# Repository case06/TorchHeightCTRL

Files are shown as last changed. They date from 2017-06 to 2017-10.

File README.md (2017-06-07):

# TorchHeightCTRL
Capacitive height-controller for the OpenSourceEcology.org TorchTable

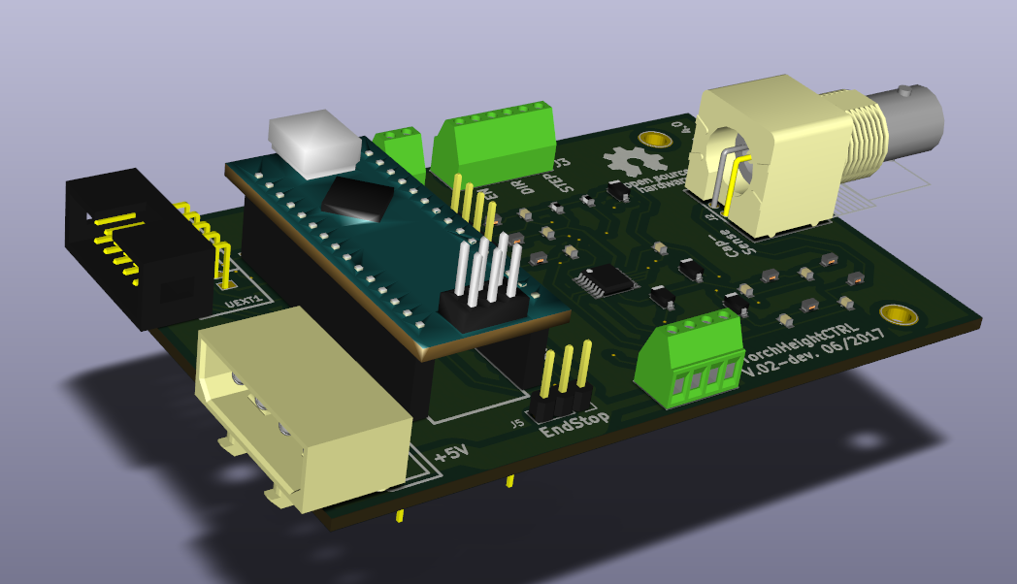
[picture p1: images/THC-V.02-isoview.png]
TorchHeightCTRL PCB
<p></p>

see also http://opensourceecology.org/wiki/CNC_Torch_Table_Height_Controller

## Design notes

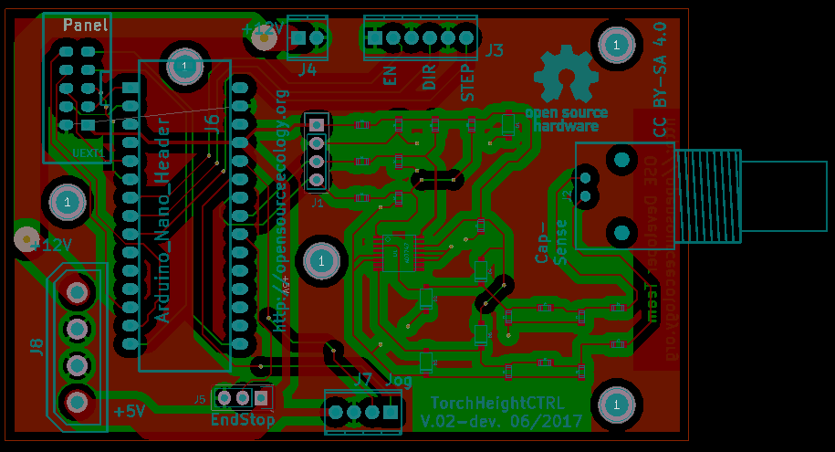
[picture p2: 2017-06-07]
images/THC-V.02-pcb.png

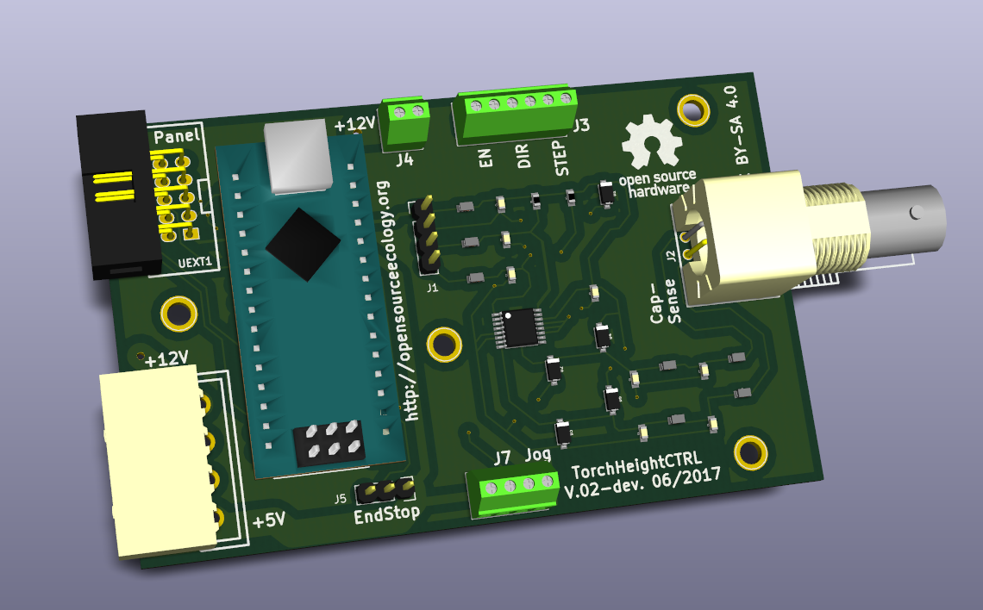
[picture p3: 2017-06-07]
images/THC-V.02-topview.png

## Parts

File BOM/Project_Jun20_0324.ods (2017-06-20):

TORCHHEIGHTCTRL02
Mouser No | Mfr. No | Manufacturer | Customer No | Description | RoHS | Lifecycle | Order Qty. | Price (EUR) | Ext.: (EUR)
78-MMSZ5233B-E3-08 | MMSZ5233B-E3-08 | Vishay |  | Zener Diodes 6.0 Volt 0.5W 5% | RoHS Compliant |  | 1 | 0,179 € | 0,18 €
71-CRCW0603J-4.7K-E3 | CRCW06034K70JNEA | Vishay |  | Thick Film Resistors - SMD 1/10watt 4.7Kohms 5% | RoHS Compliant By Exemption |  | 1 | 0,09 € | 0,09 €
571-5-146280-3 | 5-146280-3 | TE Connectivity |  | Headers & Wire Housings 3P HEADER GOLD 15u single row | RoHS Compliant |  | 1 | 0,349 € | 0,35 €
810-MMZ1608R102A | MMZ1608R102A | TDK |  | Ferrite Beads Ferrite Chip Beads | RoHS Compliant |  | 7 | 0,09 € | 0,63 €
571-826629-4 | 826629-4 | TE Connectivity |  | Headers & Wire Housings 4P SINGLE ROW | RoHS Compliant |  | 1 | 0,439 € | 0,44 €
863-MMSD701T1G | MMSD701T1G | ON Semiconductor |  | Schottky Diodes & Rectifiers 70V 225mW Single | RoHS Compliant |  | 4 | 0,349 € | 1,40 €
609-251R14S0R5BV4T | 251R14S0R5BV4T | Johanson |  | Multilayer Ceramic Capacitors MLCC - SMD/SMT 250volts 0.5pF ULTRA HIGH Q NPO | RoHS Compliant |  | 2 | 0,215 € | 0,43 €
810-C1608C0G1H0R5C | C1608C0G1H0R5C080AA | TDK |  | Multilayer Ceramic Capacitors MLCC - SMD/SMT 0603 0.5pF 50V C0G 0.25pF | RoHS Compliant | NRND | 2 | 0,098 € | 0,20 €
810-C1608C0G1H100D | C1608C0G1H100D080AA | TDK |  | Multilayer Ceramic Capacitors MLCC - SMD/SMT 0603 10pF 50volts C0G +/-0.5pF | RoHS Compliant | NRND | 2 | 0,26 € | 0,52 €
81-GRM18R60J225KE19D | GRM188R60J225KE19D | Murata |  | Multilayer Ceramic Capacitors MLCC - SMD/SMT 0603 2.2uF 6.3volts X5R 10% | RoHS Compliant |  | 2 | 0,143 € | 0,29 €
651-1725672 | 1725672 | Phoenix Contact |  | Fixed Terminal Blocks 4P 2.54mm 90DEG | RoHS Compliant |  | 1 | 2,69 € | 2,69 €
651-1725698 | 1725698 | Phoenix Contact |  | Fixed Terminal Blocks 6P 2.54mm 90DEG | RoHS Compliant |  | 1 | 3,95 € | 3,95 €
651-1725656 | 1725656 | Phoenix Contact |  | Fixed Terminal Blocks 2P 2.54mm 90DEG | RoHS Compliant |  | 1 | 1,34 € | 1,34 €
855-M20-7821546 | M20-7821546 | Harwin |  | Headers & Wire Housings 15 PIN SIL VERTICAL SOCKET TIN | RoHS Compliant |  | 2 | 1,35 € | 2,70 €
538-90130-3110 | 90130-3110 | Molex |  | Headers & Wire Housings HDR DUAL R/A 10P shrouded fully load | RoHS Compliant |  | 1 | 1,13 € | 1,13 €
651-1757035 | 1757035 | Phoenix Contact |  | Pluggable Terminal Blocks 4 Pos 5.08mm pitch Plug 24-12 AWG Screw | RoHS Compliant |  | 1 | 3,23 € | 3,23 €
651-1759033 | 1759033 | Phoenix Contact |  | Pluggable Terminal Blocks 4 Pos 5.08mm pitch Through Hole Header | RoHS Compliant |  | 1 | 1,15 € | 1,15 €
571-1-1634612-0 | 1-1634612-0 | TE Connectivity |  | RF Connectors / Coaxial Connectors PCB Skt 50Ohm MP Black | RoHS Compliant By Exemption |  | 1 | 1,62 € | 1,62 €
This orderlist is available as mouser-project:
http://www.mouser.de/tools/projectcartsharing.aspx
project-access-ID: 64fff8ecbf

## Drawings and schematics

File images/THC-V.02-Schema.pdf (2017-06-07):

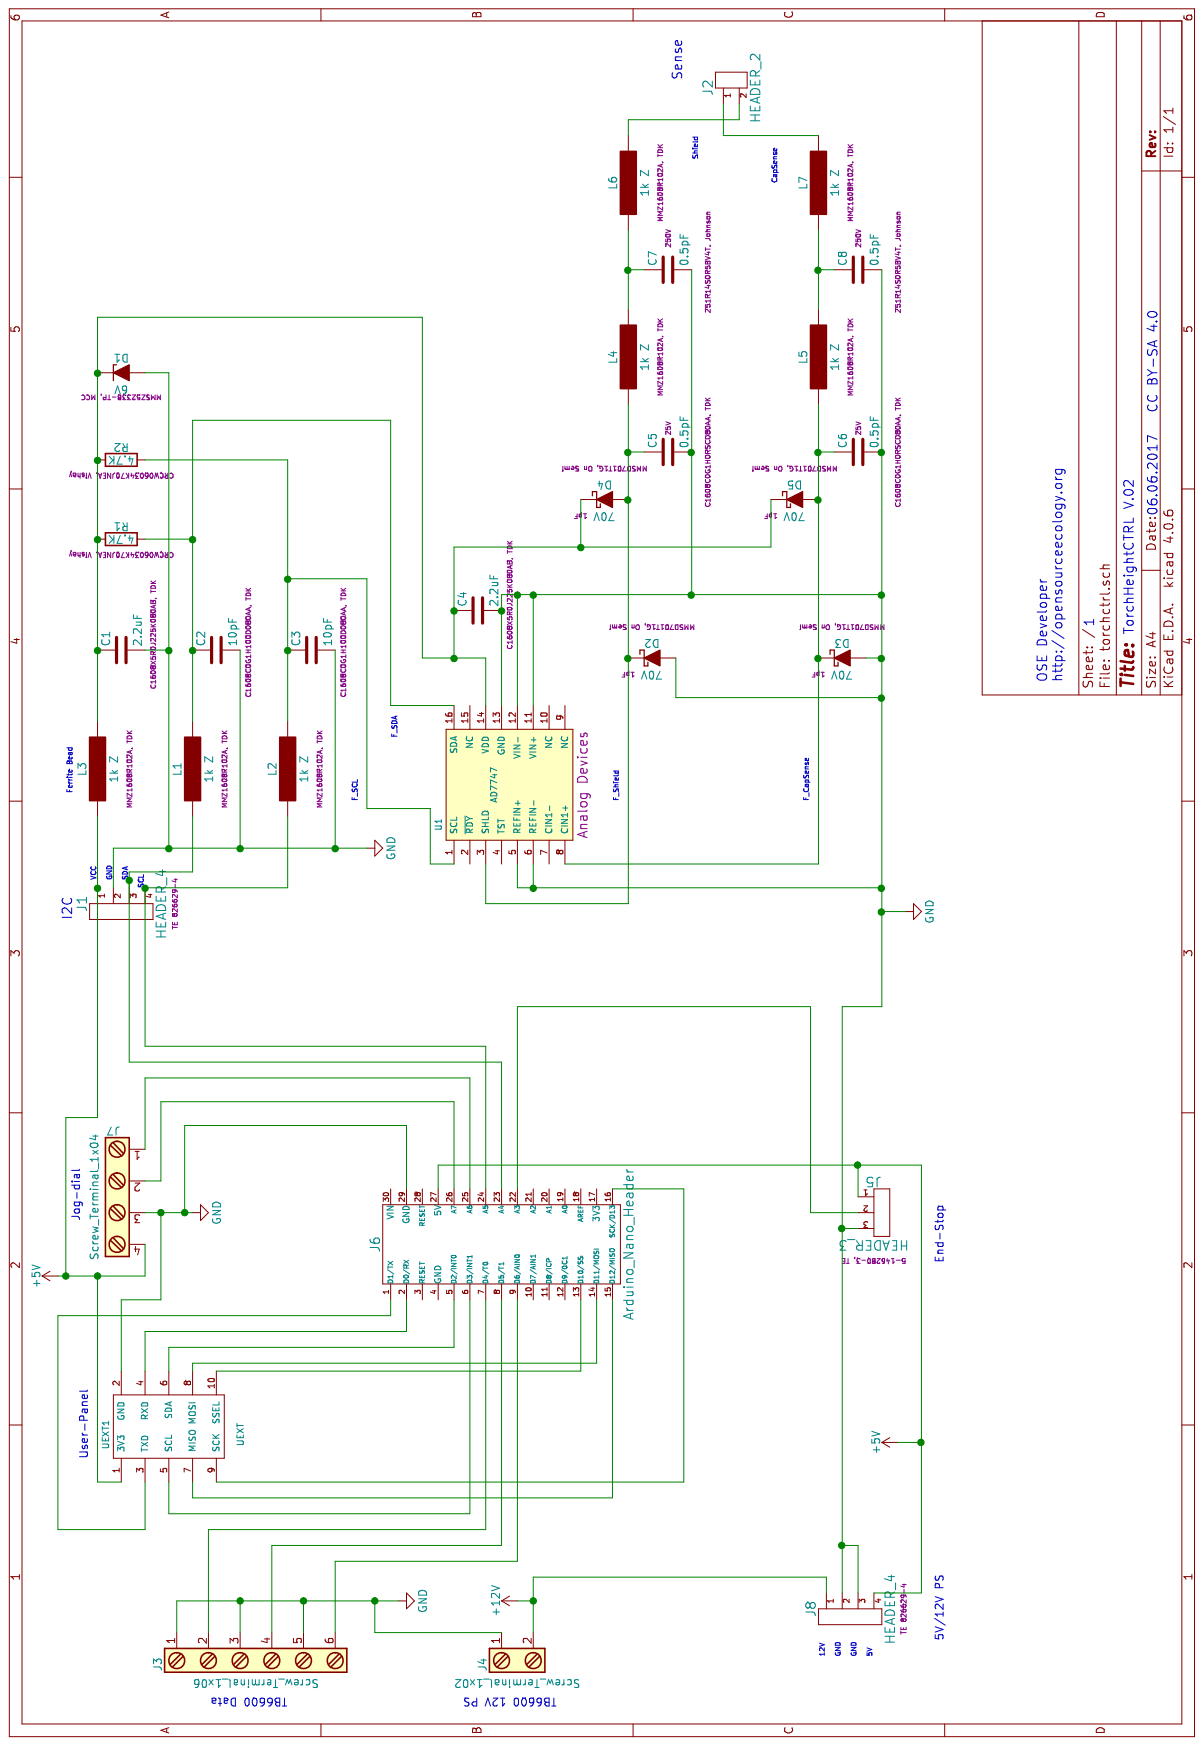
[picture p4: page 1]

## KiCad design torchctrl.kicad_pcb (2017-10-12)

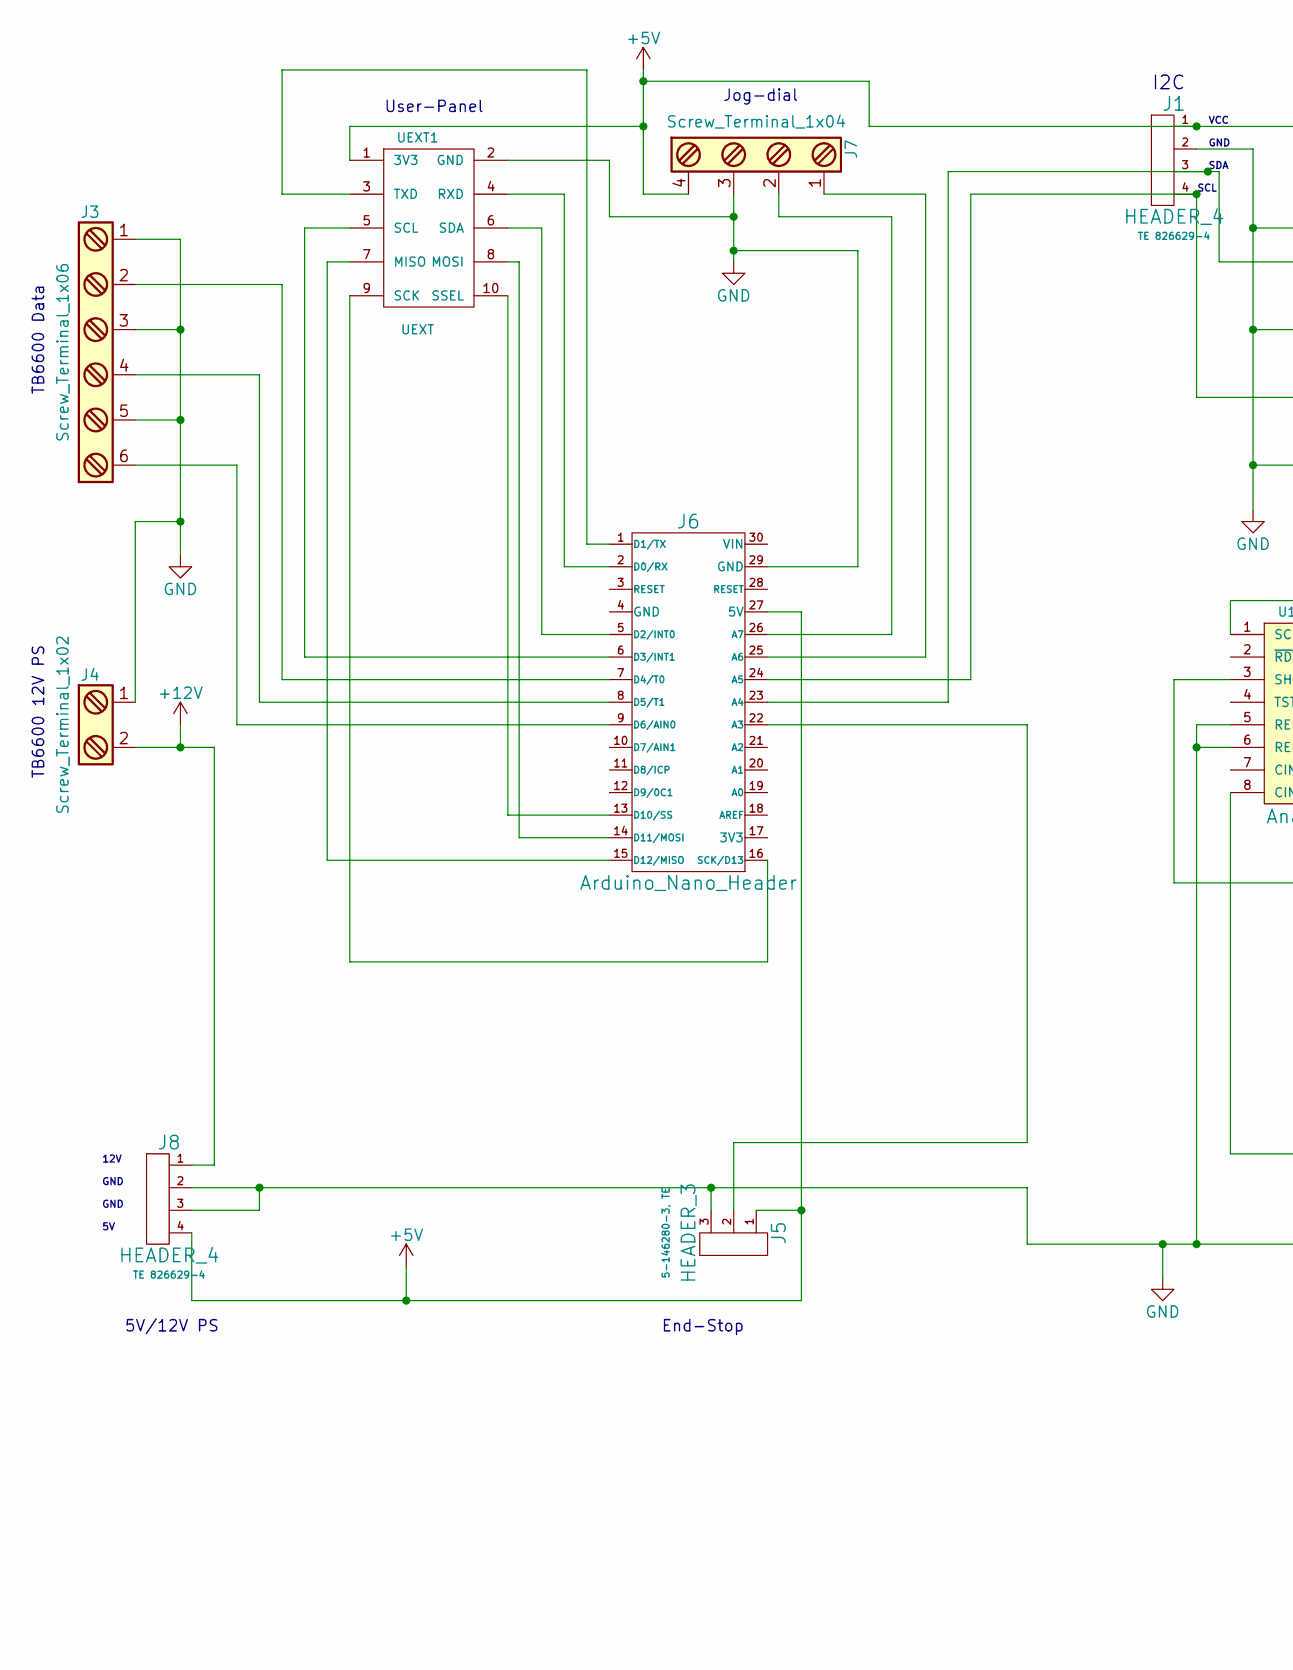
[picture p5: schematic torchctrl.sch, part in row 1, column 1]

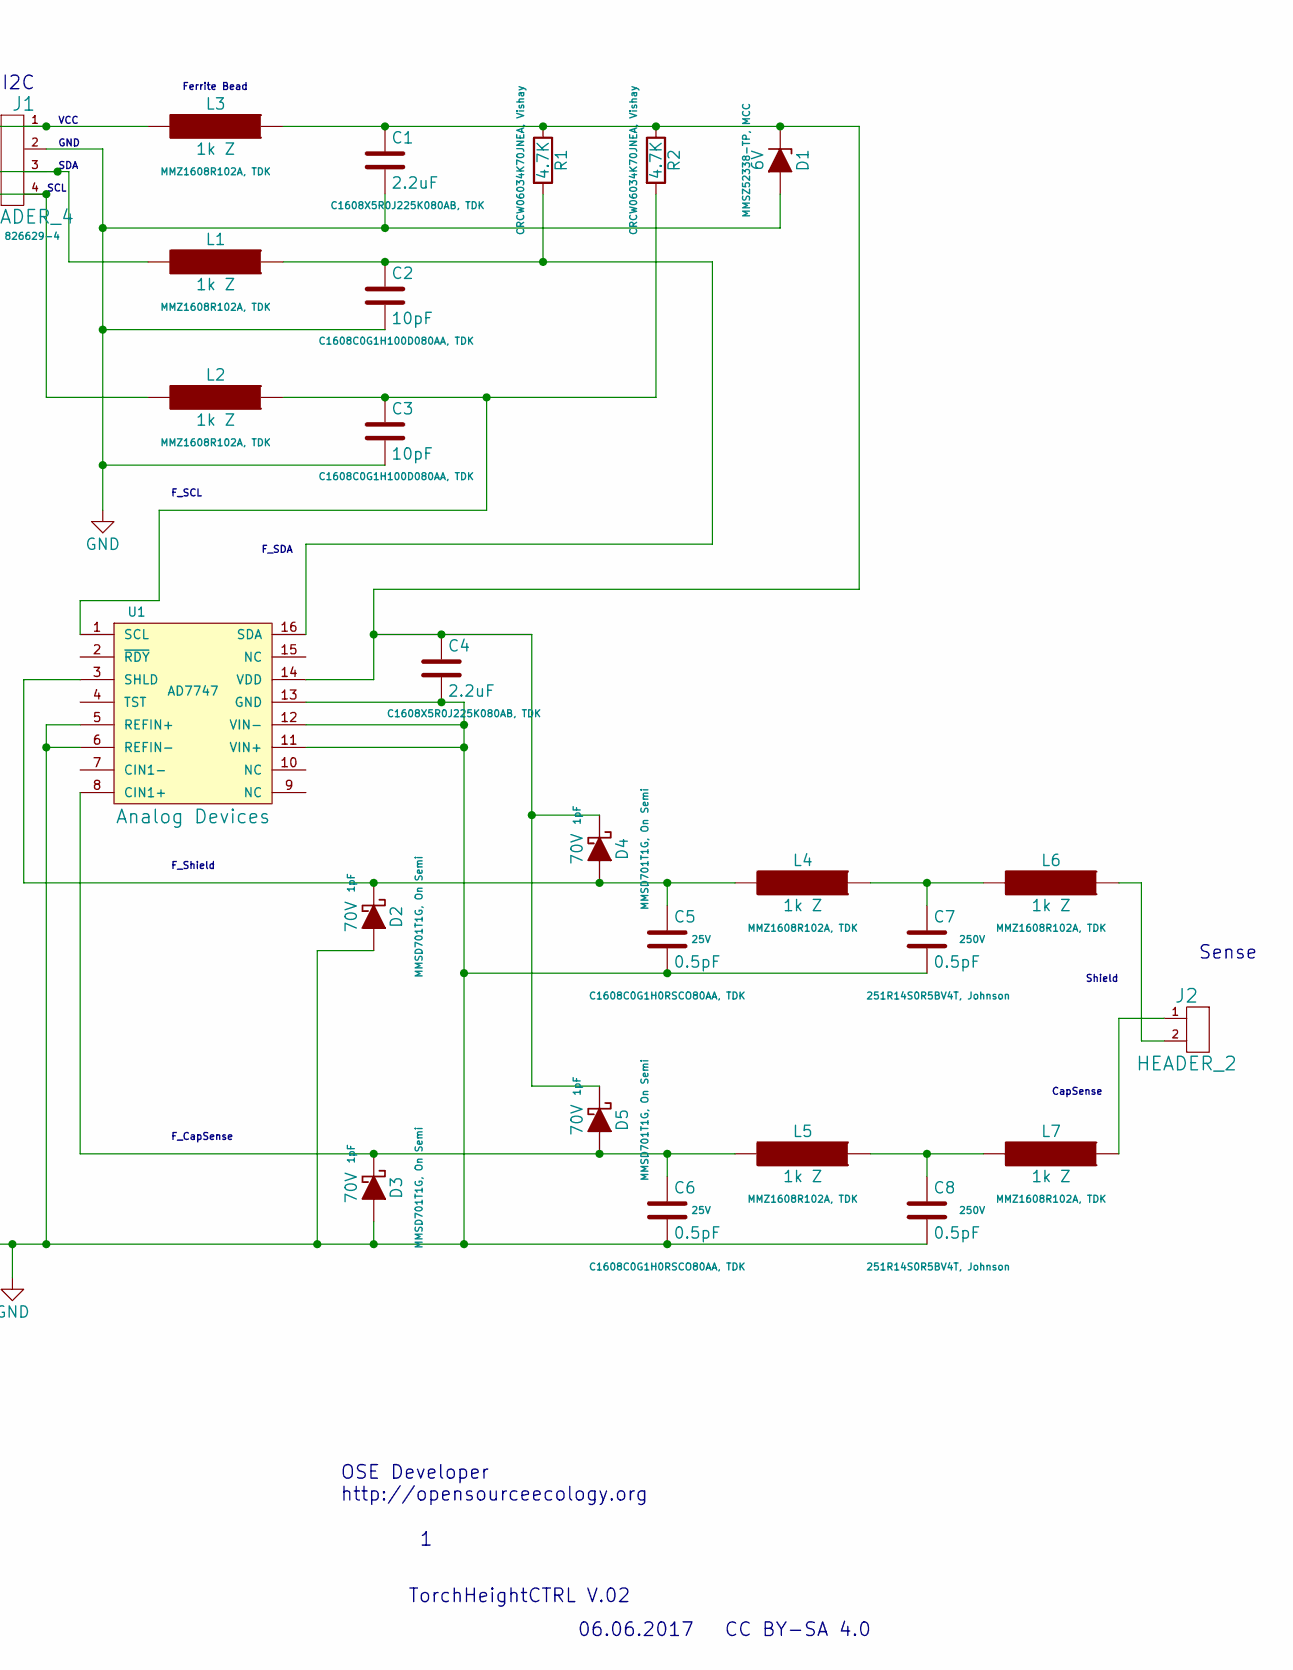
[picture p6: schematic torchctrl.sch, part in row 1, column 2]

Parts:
C1, C4: 2.2uF; c_0603
C2, C3: 10pF; c_0603
C5, C6, C7, C8: 0.5pF; c_0603
D1: 6V; sod123
D2, D3, D4, D5: 70V; sod123
J1: HEADER_4; Pin_Header_Straight_1x04
J2: HEADER_2; bnc_90_1-1337543-0
J3: Screw_Terminal_1x06; mpt_0,5%2f6-2,54
J4: Screw_Terminal_1x02; mpt_0,5%2f2-2,54
J5: HEADER_3; Pin_Header_Straight_1x03
J6: Arduino_Nano_Header; arduino_mini
J7: Screw_Terminal_1x04; mpt_0,5%2f4-2,54
J8: HEADER_4; conn_hdd_15-24-4449
L1, L2, L3, L4, L5, L6, L7: 1k Z; r_0603
R1, R2: 4.7K; r_0603
U1: AD7747; tssop-16
UEXT1: UEXT; vasch_strip_5x2

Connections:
+5V: J1.1, J5.1, J6.27 (5V), J7.4, J8.4, L3.2, UEXT1.1 (3V3)
+12V: J4.2, J8.1
GND: C1.2, C2.2, C3.2, C4.2, C5.2, C6.2, C7.2, C8.2, D1.2 (A), D2.2 (A), D3.2 (A), J1.2, J3.1, J3.3, J3.5, J4.1, J5.3, J6.29 (GND), J7.3, J8.2, J8.3, U1.5 (REFIN+), U1.6 (REFIN-), U1.11 (VIN+), U1.12 (VIN-), U1.13 (GND), UEXT1.2 (GND)
unnamed: C1.1, C4.1, D1.1 (K), D4.1 (K), D5.1 (K), L3.1, R1.1, R2.1, U1.14 (VDD)
unnamed: C2.1, L1.1, R1.2, U1.16 (SDA)
unnamed: C3.1, L2.1, R2.2, U1.1 (SCL)
unnamed: C5.1, D2.1 (K), D4.2 (A), L4.2, U1.3 (SHLD)
unnamed: C6.1, D3.1 (K), D5.2 (A), L5.2, U1.8 (CIN1+)
unnamed: C7.1, L4.1, L6.2
unnamed: C8.1, L5.1, L7.2
unnamed: J1.3, J6.23 (A4), L1.2
unnamed: J1.4, J6.24 (A5), L2.2
unnamed: J2.1, L7.1
unnamed: J2.2, L6.1
unnamed: J3.2, J6.7 (D4/T0)
unnamed: J3.4, J6.8 (D5/T1)
unnamed: J3.6, J6.9 (D6/AIN0)
unnamed: J5.2, J6.22 (A3)
unnamed: J6.1 (D1/TX), UEXT1.3 (TXD)
unnamed: J6.2 (D0/RX), UEXT1.4 (RXD)
unnamed: J6.5 (D2/INT0), UEXT1.6 (SDA)
unnamed: J6.6 (D3/INT1), UEXT1.5 (SCL)
unnamed: J6.13 (D10/SS), UEXT1.10 (SSEL)
unnamed: J6.14 (D11/MOSI), UEXT1.8 (MOSI)
unnamed: J6.15 (D12/MISO), UEXT1.7 (MISO)
unnamed: J6.16 (SCK/D13), UEXT1.9 (SCK)
unnamed: J6.25 (A6), J7.1
unnamed: J6.26 (A7), J7.2

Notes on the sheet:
TorchHeightCTRL V.02
06.06.2017
OSE Developer http://opensourceecology.org
CC BY-SA 4.0
I2C
Ferrite Bead
Sense
CapSense
Shield
F_Shield
F_CapSense
F_SCL
F_SDA
VCC
GND
SDA
SCL
Jog-dial
TB6600 Data
TB6600 12V PS
User-Panel
End-Stop
5V/12V PS
12V

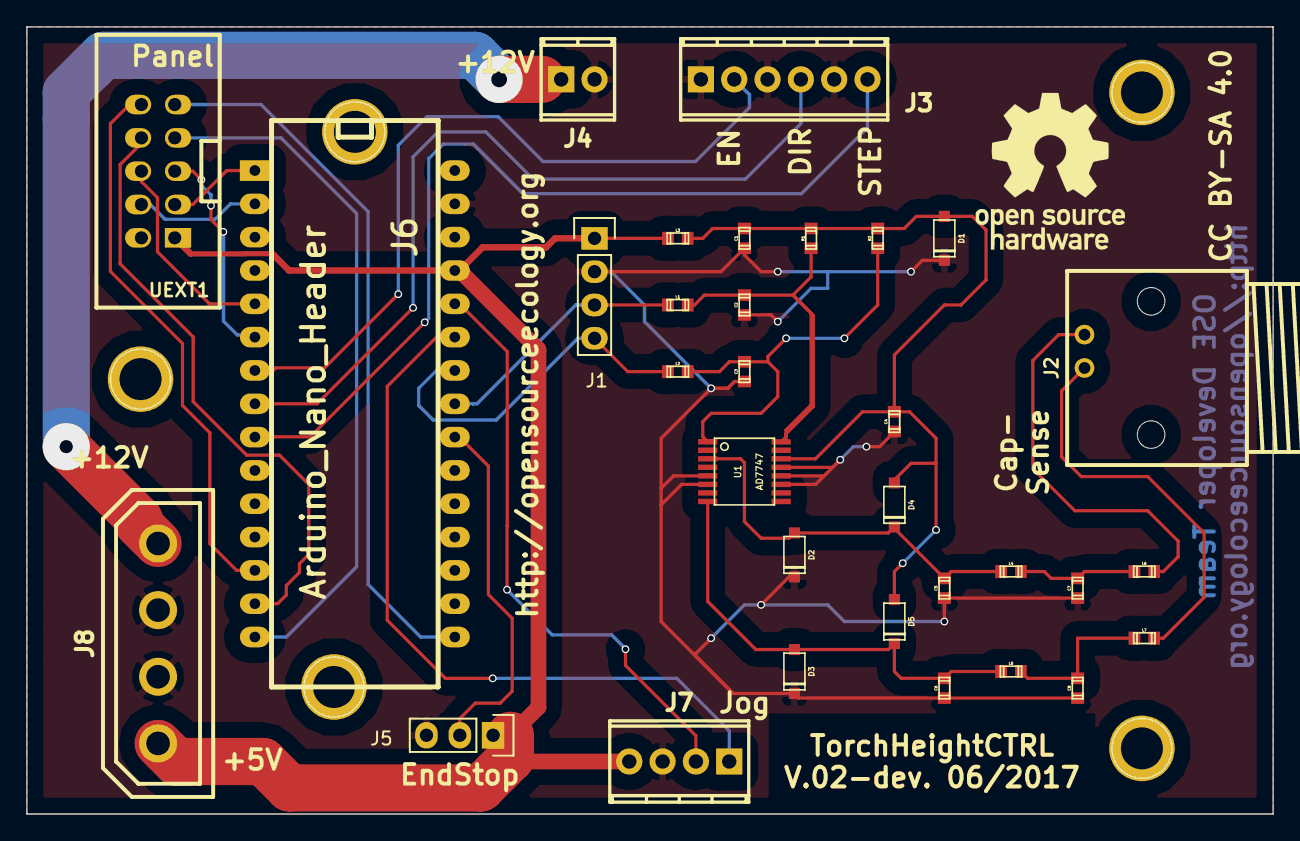
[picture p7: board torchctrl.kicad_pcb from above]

Board: 2 copper layers, 95.0 x 60.0 mm, 32 parts (0 on the bottom side), 28 nets.

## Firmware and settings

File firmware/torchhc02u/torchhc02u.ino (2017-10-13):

/*==================================================================

TorchHeightCTRL  V.02

Torchtable-Heightcontroller for Arduino-Nano,
and TB6600 Stepper-Driver, with jogwheel and cap-sense

see
http://opensourceecology.org/wiki/CNC_Torch_Table_Z_Height_Control
http://opensourceecology.org/wiki/CNC_Torch_Table_Height_Controller
 
by Case06 10.08.2017,       CC BY SA 4.0

=====================================================================*/
 
// Aidan Williamson code from 11.07.2014
// see http://opensourceecology.org/wiki/Aidan_Williamson_Log_2014#7.2F9
//
//----------------------------------------------------------------------------------------
//|     AD7747 Capacitive Sensor                                                         |
//|   Based on code by  MiG found at:http://forum.arduino.cc/index.php/topic,11882.0.html|                                           |
//|                                                                                      |
//|  Author: Aidan Williamson (although I didn't do much original work)                  |
//|  Written: 7/3/2014                                                                   |
//|  ad7747 datasheet:http://www.analog.com/static/imported-files/data_sheets/AD7747.pdf |
//|                                                                                      |
//|                                                                                      |
//|                                                                                      |
//|                                                                                      |
//-----------------------------------------------------------------------------------------


#include <Wire.h>                  //include the library for i2c communication



// Stepper-Driver
int PUL=6; // D6, Pin9, define Pulse pin
int DIR=5; // D5, Pin8, define Direction pin
int ENA=4; // D4, Pin7, define Enable Pin


// Rotary Encoder (eg. KY-040)
// Warning: The Arduino Nano analog ports A6 and A7
// can NOT be used as digital-input-ports, like A0 to A5.
// see https://forum.arduino.cc/index.php?topic=123176.0
// and there https://forum.arduino.cc/index.php?topic=123176.msg1586523#msg1586523
// as a workaround.
int pinA = A6;  // Pin25 Connected to CLK on KY-040
int pinB = A7;  // Pin26 Connected to DT on KY-040
int pinStateA6 = 0;
int pinStateA7 = 0; 
// int pinC = A3;  // Pin22 Connected to SW on KY-040  (normally used for Endstop (!!!))
int pinKnob = 12;  // D12 Connected to SW on KY-040  (Workaround, this pin is normally used by UEXT expansion port (!!!))
int encoderPosCount = 0; 
int pinALast;  
int aVal;
boolean bCW;


// EndStop
int pinEndStop = A3;
int endstop = 1;  // 1 = open , 0 = closed contact
int goDir = 0;  // Direction to go:  0 = upward,  1 = downward



// handling
int diff = 0;
int steps = 0;
int switchmode = 0;   // toggles between 0 = manual mode and 1 = autobalancing mode

// verbose-mode toggles debug-messages on the serial monitor
// 0 = silent
// 1 = output only the raw-data, for host-monitor-tool
// 2 = setup-values (calibration etc.)
// 3 = absolute position and target working-height
// 4 = balancing data
// 9 = all messages
int verbose = 2;    



// CapSense     
//int capreadybit = (bitRead(TWDR,0));  //initialize variable readybit to be two wire data register's lsb

# define RANGE 30.0000000000    // Range in MilliMeters
# define TARGET 15.0000000000    // Default working height Target value is 15mm above ground
# define NSAMPLES 4  // how many samples for averaging

// float offset=8.192100; // value from datasheet
float offset=8.192;
float lastcapf = 0.00;   // last measured capacitance
float mincapf = 0.00;   // lowest distance to the surface; either hand_adjusted or given as home-position from EndStop
float maxcapf = 0.00;   // widest distance

float minattof = 0.00;
float maxattof = 0.00;
//float rangeattof = 0.00;
float targetdistanceaf = 0.00;
float target = TARGET;

float range = 0.00;  // the distance-range in attoFarad
float camm = 0.00;  // the capacitance per millimeter in attoFarad



// Movements

int distanceSteps = 40 * RANGE;  // how many steps along the whole range; 1 step is 25 microns, so 40 steps are 1 mm
// float targetdistance = 0.00;  // contains the balancing-height-value as target-capacitance in pF
float toohigh = 0.00;
float toolow = 0.00;
int upsteps = 0;
int downsteps = 0;
float f = 0.00; 
float nsamples[NSAMPLES];
float slidav = 0.00;   // sliding average
// float fori = 0.00;
int pos_changed = 0;

float pos = 0.00; // current height position in mm
float distance2go = 0.00;;
int steps2go = 0;  // 1 step is 25 microns, so 1mm is 40 steps



    
void setup()
{
  
  delay(3000);
  
  //nsamples = new float[NSAMPLES];
  
  // TB6600 setup
  pinMode (PUL, OUTPUT);
  pinMode (DIR, OUTPUT);
  pinMode (ENA, OUTPUT);

  // Rotary Encoder setup
  pinMode (pinA,INPUT);
  pinMode (pinB,INPUT);
  pinMode (pinKnob,INPUT_PULLUP); // Knob
//  pinMode (pinKnob,INPUT); // Knob
  // EndStop setup
  pinMode (pinEndStop,INPUT);
  
   
  // Read Pin A; Whatever state it's in will reflect the last position
  // pinALast = digitalRead(pinA);  
  pinStateA6 = analogRead(A6) > 100 ? 0 : 1;
  pinALast = pinStateA6;  


  Serial.begin (115200);
     
  digitalWrite(ENA,LOW);  // steppers always activated
   
  // Default step-width. When in 1/8-Microstepping mode then a 
  // value of 1 results into a movement of 25 microns step-width
  // (, but you can set it also to bigger values)
  steps = 1;
  
/*  
  
  // CapSense setup 
  Wire.begin();                   //sets up i2c for operation

  Wire.beginTransmission(0x48);
  Wire.write(0xBF);
  Wire.write(0x00);
  Wire.endTransmission();
  delay(4);
  Wire.beginTransmission(0x48);   // begins write cycle
  Wire.write(0x07);              //address pointer for cap setup register
  Wire.write(0xA0);              //b'10100000' found from datasheet page 16
  Wire.endTransmission();        //ends write cycle
  delay(4);                      // Wait for data to clock out? I'm not 100% sure why this delay is here (or why it's 4ms)
  Wire.beginTransmission(0x48);   //begins transmission again
  Wire.write(0x09);              //address pointer for capacitive channel excitation register
  Wire.write(0x0E);              //recommended value from datasheet
  Wire.endTransmission();
  delay(4);  
  Wire.beginTransmission(0x48);
  Wire.write(0x0A);              //address pointer for the configuration register
  Wire.write(0x21);              //b'00100001' for continuous conversion, arbitrary VTF setting, and mid-range capacitive conversion time
  Wire.endTransmission();
  Wire.beginTransmission(0x48);
  Wire.write(0x0B);              //CAP DAC A Register address (Positive pin data)
  Wire.write(0x80);               //b'10111111' for enable Cap DAC A
  Wire.endTransmission();
  // Serial.println("Hello!");        //test to make sure serial connection is working
  
  
  digitalWrite(DIR,HIGH); // go downward for homing
  goDir = 1;
  
  // ======
  // Homing
  // ======
  if((verbose == 2) || (verbose == 3)) Serial.print("Start Homing ..."); 
  while(endstop == 1)
  {
    doSteps(1);
    delay(10);  // dont know why this delay is needed ... but it is.
  }
  if((verbose == 2) || (verbose == 3)) Serial.println("... Homing done !"); 
  

  // ===========    
  // Calibration
  // ===========
  if((verbose == 2) || (verbose == 3)) Serial.print("Start Calibration ..."); 
  delay(100);
  pos = 0.00;   // initial position after homing
  target = TARGET; // initial default working height after homing
  mincapf = doSample();
  delay(100);
  mincapf = doSample();  // dont know why this must happen two times.
  minattof = (mincapf-offset)*100000;


  digitalWrite(DIR,LOW); // backward (=upward), counterclockwise
  goDir = 0;
  
  // Serial.println(endstop); 
  
  doSteps(distanceSteps);

  delay(300);
  pos = 30.00;  // max-position
  target = TARGET; // initial default working height after homing
  maxcapf = doSample();
  maxattof = (maxcapf-offset)*100000;
  delay(100);
  if((verbose == 2) || (verbose == 3)) Serial.println("... Calibration done !"); 
  
  
  // =================================
  // Go back to default working height
  // =================================

  target = TARGET;
  if((verbose == 2) || (verbose == 3) || (verbose == 9))
  {
    Serial.println("Go down to default working height: ");
    Serial.print(target,3);

    Serial.print(" from pos: ");
    Serial.println(pos,3);
  }
  
  digitalWrite(DIR,HIGH); // forward (= downward)
  goDir = 1;

  distance2go = pos - target;
  distance2go = distance2go * 40;  // 1 step is 25 microns, so 1mm is 40 steps
  // steps2go = (int) distance2go;  // When casting from a float to an int, the value is truncated not rounded.  (!)
  steps2go = round(distance2go);
  
  if((verbose == 2) || (verbose == 3) || (verbose == 9))
  {
    Serial.print("  ==> calculated steps: ");
    Serial.println(steps2go);
  }

  doSteps(steps2go);
  target = TARGET;
  verbose = 3;
  
  
  
  
  
  // ============================
  // Calculate calibration values
  // ============================
  range = mincapf - maxcapf;
  // // targetdistance = range / RANGE * target;
  // // targetdistance = maxcapf + targetdistance;  
  range = range * 100000; // attoFarad
  targetdistanceaf = range / RANGE * target;
   
  camm = range / RANGE ; 

  if((verbose == 2) || (verbose == 3))
  { 
    Serial.print("min: ");
    Serial.print(mincapf,DEC);
    Serial.print("  max: ");
    Serial.println(maxcapf,DEC);

    Serial.print("min aF: ");
    Serial.print(minattof,DEC);
    Serial.print("  max aF: ");
    Serial.print(maxattof,DEC);

    Serial.print("  range: ");
    Serial.print(range,DEC);

    Serial.print(" aF ==>   aF/mm: ");
    Serial.print(camm,DEC);

    Serial.println();
  
    // Serial.print("TargetCapacitance: ");
    // Serial.println(targetdistance,DEC);

    Serial.print("TargetCapacitance_aF: ");
    Serial.println(targetdistanceaf,DEC);

    Serial.print("target/mm: ");
    Serial.println(target,3);
  
    Serial.println("-----------");
  }





  // =====================================
  // Set initial value for sliding average
  // =====================================
    
  lastcapf = getNextSample();
  f= lastcapf - offset;
  f=f * 100000;  // ==> atto-Farad
  slidav = f;   // sliding average, initial value
  
  */
  
  switchmode = 0;
  
} // end of setup()
     
     
/*
float targetdistance_in_aF()
{
  // range = mincapf - maxcapf;
  // range = range * 100000; // attoFarad
  targetdistanceaf = range / RANGE * target;
  return targetdistanceaf;
}  
*/

 
int getRotaryEncoder() 
 { 
   
   int stepDiff = 0;
   
   
   
   
   // aVal = digitalRead(pinA);
   pinStateA6 = analogRead(A6) > 100 ? 0 : 1;
   aVal = pinStateA6;  
  
   
   if (aVal != pinALast)
   { // Means the knob is rotating
     // if the knob is rotating, we need to determine direction.
     // See also http://henrysbench.capnfatz.com/henrys-bench/arduino-sensors-and-input/keyes-ky-040-arduino-rotary-encoder-user-manual/
     // We do that by reading pin B.
     // if (digitalRead(pinB) != aVal) 
     // if (digitalRead(pinB) == aVal) 
     
     // if (digitalRead(pinB) == aVal) 
     pinStateA7 = analogRead(A7) > 100 ? 0 : 1;
     if (pinStateA7 == aVal) 
     {  // Means pin A Changed first - We're Rotating Clockwise
       encoderPosCount ++;
       bCW = true;
       stepDiff = 1;
     } 
     else 
     {// Otherwise B changed first and we're moving CCW
       bCW = false;
       encoderPosCount--;
       stepDiff = -1;
     }
     /*
     Serial.print ("Rotated: ");
     if (bCW) { Serial.println ("clockwise"); }
     else { Serial.println("counterclockwise"); }
     Serial.print("Encoder Position: ");
     */
//     Serial.print(encoderPosCount);
//     Serial.print("  |  ");
     
   } else stepDiff = 0; // means: knob is not rotated
   
   pinALast = aVal;
   // return encoderPosCount;
   return stepDiff;
 }  // end getRotaryEncoder() 
 

 void doSteps(int numsteps)
 {
     
    for (int i=0; i< numsteps; i++)  
    {
       // check EndStop
       endstop = digitalRead(pinEndStop);
        
       if((endstop == 1) || ((endstop == 0) && (goDir == 0)))
       {
         digitalWrite(PUL,HIGH);
         delayMicroseconds(50);
         digitalWrite(PUL,LOW);
         delayMicroseconds(50);
         
         // update positioncounter
         if(goDir == 0)  // go upward
         {
           pos = pos + 0.0250000000;
           if(switchmode == 0) target = target + 0.0250000000;
         }  
         else   // go downward
         {  
           pos = pos - 0.0250000000;
           if(switchmode == 0) target = target - 0.0250000000;
         }  
         pos_changed = 1;  
           
       }
       else pos = 0.0000000000;  // end if endstop  
       
       
       if((verbose == 3) || (verbose == 9))
       {
         Serial.print("pos: ");
         Serial.print(pos,3);
         Serial.print("  target: ");
         Serial.println(target,3);
       }
       // else Serial.println("condition not fullfilled");
    } // end for
 } // end doSteps()
 

 
float doSample()
{ 
  
  float capf = 0.00;
  
  // CapSense with AD7747
  Wire.beginTransmission(0x48);   //talking to chip
  Wire.write(byte(0x00));                  //status register address
  Wire.endTransmission();
  Wire.requestFrom(0x48,1);       //request status register data
  int readycap;
  
  readycap=Wire.read();
  if((readycap&0x1)==0)
  {                // ready?
    Wire.beginTransmission(0x48); //arduino asks for data from ad7747
    Wire.write(0x01);             //set address point to capacitive DAC register 1
 
    Wire.endTransmission();       //pointer is set so now we can read the data
 
    Wire.requestFrom(0x48,3);     //reads data from cap DAC registers 1-3
 
    while(Wire.available())
    {
      unsigned char hi,mid,lo;      //1 byte numbers
      long capacitance;            //will be a 3byte number
      float pf;                    //scaled value of capacitance
      hi=Wire.read();
      mid=Wire.read();
      lo=Wire.read();
      capacitance=(hi<<16)+(mid<<8)+lo-0x800000;
      pf=(float)capacitance*-1/(float)0x800000*8.192f;
      //pf=pf-offset;
      //pf=pf*100000;
      capf = pf;
      if((verbose == 1) || (verbose == 9)) Serial.print(pf, DEC); //prints the capacitance data in decimal through serial port
    }
       // Serial.println("---");
       if((verbose == 1) || (verbose == 9)) Serial.println();
  } // end if
  
  return capf;
  
} // end doSample() 
 


float getNextSample()
{
  float total = 0.00;  
  lastcapf = 0.00;

  for(int i=0; i < NSAMPLES; i++)
  {
    nsamples[i] = 0.00;
    // lastcapf = lastcapf + doSample();
    int doitflag = 0;
    while(!doitflag)
    {
       lastcapf = doSample();
       if(lastcapf != 0)       // if sampling goes to fast doSample() returns 0
       { 
         nsamples[i] = lastcapf;
         doitflag = 1;
       } // end if 
    } // end while
    total = total + nsamples[i];
  } // end for 
  lastcapf = total / NSAMPLES; // Average
  
  return lastcapf;
} // end of getNextSample()

 
 void loop()
{

  // check EndStop
  endstop = digitalRead(pinEndStop);
   // Serial.println(endstop);
  
  
  // check switchmode
  if(digitalRead(pinKnob) == LOW)  // Knob pressed
  {
    delay(300);  // for debouncing. maybe better: https://github.com/mathertel/OneButton
    // toggle switchmode
    if(switchmode == 1) switchmode = 0; 
    else switchmode = 1; 
    
    if((verbose == 3) || (verbose == 9))
    {
      Serial.print("Button pressed, new switchmode : ");
      Serial.println(switchmode);
    }
  } 
  
  
// auto-balancing and capsensing-mode  
if(switchmode == 1)
{
  
  delay(10); 
  // interesting: a bigger delay here doesnt necessarily lead to better repeatability-correctness; 
  // maybe holding(-torque) of stepper induces more noise than while running ?
  // Or there are maybe motor-positions which induce less noise than others ?
  lastcapf = getNextSample(); 
  
  
  
  if(lastcapf != 0)
  {
    f= lastcapf - offset;
    f=f * 100000;  // ==> atto-Farad
    
    if(pos_changed == 0)
    {
      slidav = ((slidav * 3) + f) / 4;   // sliding average
      f = slidav;
    }
    else slidav = f;  // get new position for sliding average, otherwise sliding average will thinn out the next move

    pos_changed = 0;


    targetdistanceaf = range / RANGE * target;  // range is capacitance-range measured during calibration
    
    if((verbose == 3) || (verbose == 4) || (verbose == 9))
    {
      Serial.print("pos: ");
      Serial.println(pos,3);
      Serial.print("target: ");
      Serial.println(target,3);
      
      // Serial.print("targetdistanceaf: ");
      // Serial.println(targetdistanceaf,DEC);

      // Serial.print("maxattof: ");
      // Serial.println(maxattof,DEC);

      // Serial.print("minattof: ");
      // Serial.println(minattof,DEC);

      // Serial.print("   |   calc: ");
      Serial.print("calc: ");
      // Serial.print("   |   target-capacity (calculated): ");
      // Serial.println(maxattof + targetdistanceaf,DEC);
      Serial.println(minattof - targetdistanceaf,3);
      
      // Serial.print( "  measured f: ");
      Serial.print( "sample: ");
      Serial.println(f,3);
      Serial.println( "---");
    }


    // if(f > (maxattof + targetdistanceaf)) // go upward
    if(f > (minattof - targetdistanceaf)) // go upward
    {
      // toolow = f - (maxattof + targetdistanceaf);
      toolow = f - (minattof - targetdistanceaf);

      
      if((verbose == 3) || (verbose == 4) || (verbose == 9))
      {
        Serial.print("Go up "); 
        Serial.println(toolow,DEC);
      }  
      
      if(toolow > 2.4)
      {
        upsteps = toolow / camm * 40;
        if((verbose == 3) || (verbose == 4) || (verbose == 9)) Serial.println(upsteps);
        digitalWrite(DIR,LOW); // backward (=upward), counterclockwise
        goDir = 0;
        doSteps(upsteps);
        // pos_changed = 1;
      }  
    }
 
    // if(f < (maxattof + targetdistanceaf)) // go downward
    if(f < (minattof - targetdistanceaf)) // go downward
    {
      // toohigh = (maxattof + targetdistanceaf) - f;
      toohigh = (minattof - targetdistanceaf) - f;
      
      if((verbose == 3) || (verbose == 4) || (verbose == 9))
      {
        Serial.print("Go down "); 
        Serial.println(toohigh,DEC);
      }  
      
      if(toohigh > 2.4)
      {
        downsteps = toohigh / camm * 40;      
        if((verbose == 3) || (verbose == 4) || (verbose == 9))  Serial.println(downsteps);
        digitalWrite(DIR,HIGH); // forward (=downward), clockwise
        goDir = 1;
        doSteps(downsteps);
        // pos_changed = 1;
                
      }
    }  
   
 
  } // end if lastcapf != 0
  
} // end if switchmode == 1



// manual mode
if(switchmode == 0)
{

  // Rotary Encoder    
  diff = getRotaryEncoder();
    
  if(diff != 0)
  {
    // Serial.print("Diff: ");
    // Serial.println(diff);
//    Serial.print(encoderPosCount * steps * 0.025);
//    Serial.println(" mm");
//    Serial.println("   ");
    
        
    if(diff == 1) 
    {
      digitalWrite(DIR,HIGH); // forward/downward, clockwise
      goDir = 1;
      // target = target - 0.025;
    }  
    else
    {
      digitalWrite(DIR,LOW); // backward/upward, counterclockwise
      goDir = 0;
      // target = target + 0.025;
    }  
    
    doSteps(steps);
  //delay(100);
  
  } // else: do nothing
 
} // end if switchmode == 0 
 
 
 
    
 } // end loop()
 
 
 

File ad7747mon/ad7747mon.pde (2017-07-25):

import processing.opengl.*;
import processing.serial.*;
import java.io.*;
import java.util.*;

// The serial port:
Serial arduinoPort;  
Thread serialThread;
int testMode = 0;
//line delimiter
int lf = 10;


int[] y;
String val;     // Data received from the serial port
float offset=8.192100;
float slidav = 0.00;  // sliding average

int viewfactor = 1;

void setup() {
  // size(viewWidth, viewHeight, OPENGL);
  size(1200, 600, OPENGL);
    smooth();
  //noStroke();

  // font = loadFont("LucidaGrande-48.vlw");
  y = new int[width];

  println(Serial.list());
  arduinoPort = new Serial(this, Serial.list()[4], 115200);
  
  
  
  
    
} // end of setup():    







void draw() 
{

  
  
  background(0); // Read the array from the end to the
  
    
  if ( arduinoPort.available() > 0) 
  {  // If data is available,
    val = arduinoPort.readStringUntil('\n');         // read it and store it in val
  } 
  println(val); //print it out in the console

  float f = float(val);
  
  // f=f - offset;
  // f=f * 100000;  // ==> milli-femto-Farad
  
  slidav = ((slidav * 3) + f) / 4;   // sliding average
  f = slidav;
  
  println(f);
  
  // beginning to avoid overwriting the data
  for (int i = y.length-1; i > 0; i--) 
  {
    y[i] = y[i-1];
  }
  // Add new values to the beginning
  //y[0] = round(f) * 4;
  y[0] = round(f) * viewfactor;
  
  println(y[0]);
  
  
 println(pixelWidth, pixelHeight);
 
  
   // draw grid
  // stroke(20, 200, 100); hellgruentuerkis
  stroke(5, 50, 25);
  // stroke(10, 100, 50);
  
  for (int i = 1; i < 58; i++) 
  {
    
    // dottedLine(0, i*10*4, width-1, i*10*4,20);
    line(0, i*10*viewfactor, width-1, i*10*viewfactor);
    text(i*10, 10, i*10*viewfactor);
  }
 text("[mfF]", 10, 590);
 
  
  
  // draw curve 
  stroke(204, 102, 0); //karminocker
  stroke(255, 194, 0); //amber
    
  // Display each pair of values as a line
  for (int i = 1; i < y.length; i++) 
  {
    
    line(i, y[i], i-1, y[i-1]);
  }
  
 
  
  // display values
  text(f, 100, 590);
  text("mfF", 160, 590);
  
  text("measured:", 830, 590);
  text(val, 900, 590);
  text("pF", 1000, 590);
  
 
  //delay(100);
  
  
  
} // end of draw()  

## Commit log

2017-06-07 remove old backup file
    [torchctrl_ohnekupfer.kicad_pcb]
2017-06-20 added gerber files
    [torchctrl-B.Cu.gbr, torchctrl-B.Mask.gbr, torchctrl-B.SilkS.gbr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]
2017-06-20 added order-list for mouser in BOM
    [Project_Jun20_0324.ods]
2017-08-08 added button-press functionality for rotary encoder
2017-08-11 added EndStop functionality
2017-08-15 updated EndStop functionality with balancing
2017-10-12 changed path for 3d-parts from home into repo-lib
    [torchctrl.kicad_pcb]
2017-10-12 changed layers on
    [torchctrl.kicad_pcb]
